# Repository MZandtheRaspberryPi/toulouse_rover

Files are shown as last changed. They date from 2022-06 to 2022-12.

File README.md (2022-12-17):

# auto_rover

this was a fun project where I made a wheeled ros based robot from scratch, including hardware, design, and substantial software for kinematics, control, and odometry (though I used existing SLAM and path planning packages).
frontal_pic

this robot has support for differential drive (with 2 driven wheels), skid steering (with 4 driven wheels), and omni wheels.

This repo is structured as a catkin workspace, so you should just clone it with submodules, and use catkin to build the workspace. Then the main entry point is:  

```
roslaunch toulouse_rover toulouse.launch wheel_config_type:=differential_drive autonomous_mode:=false
```

For autonomous mode, i often used screen as a multi-terminal utility:

```
screen -d -m -S toul -L roslaunch toulouse_rover toulouse.launch autonomous_mode:=true wheel_config_type:=fixed_pwm_speeds
```

You can find a compressed bag demo in the root of this repo, `toulouse_autonomy_demo.bag` which shows a scene of me controlling the robot and sending it forward and then turning a bit. You can also find the log outputs of this run in the root of this repo, `toulouse_autonomy.log`.  

## Demo GIFs

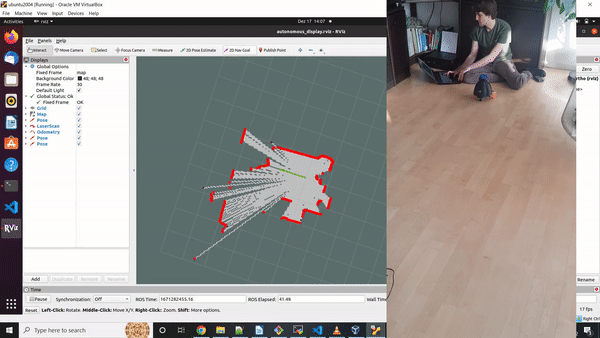
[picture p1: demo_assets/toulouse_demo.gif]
demo


## Software

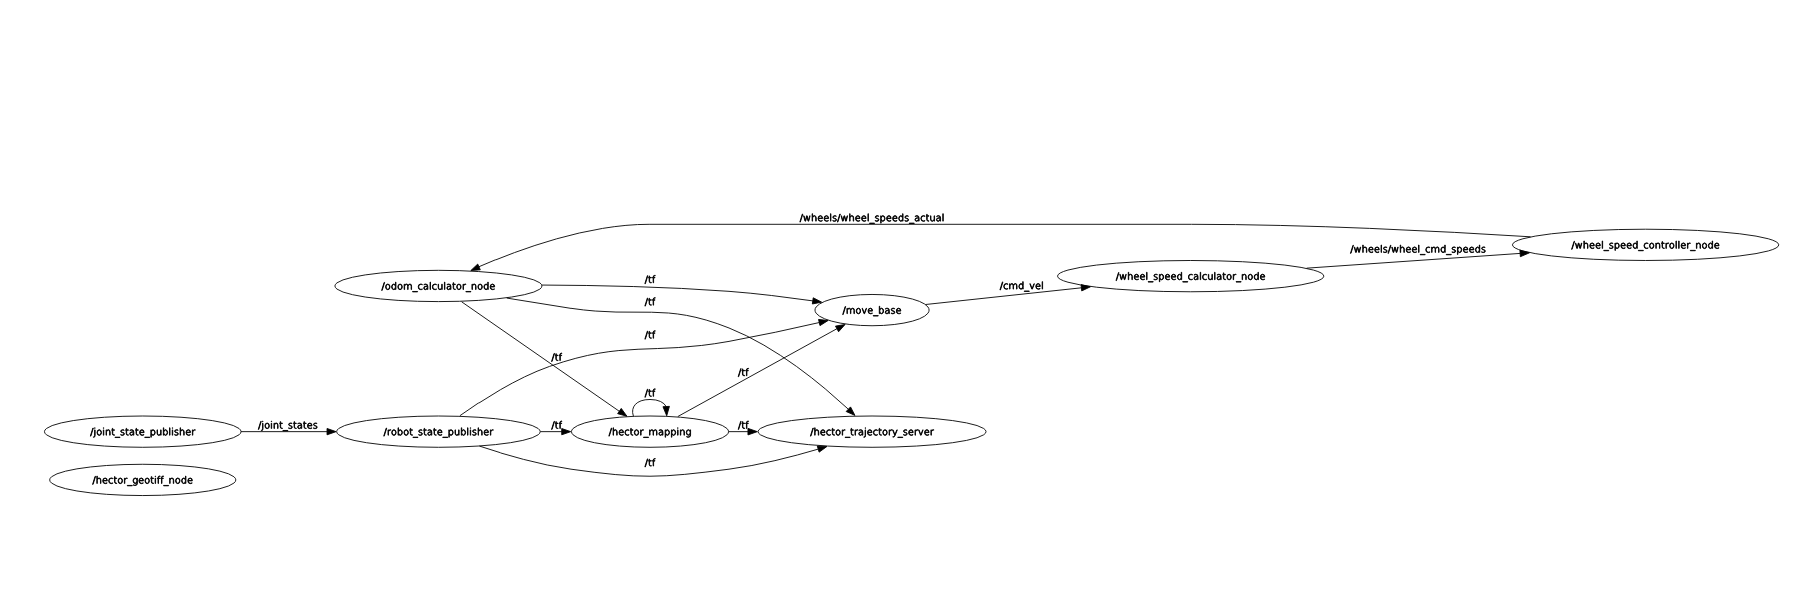
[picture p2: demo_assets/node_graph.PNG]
node_graph
  
Not pictured above is the lidar or the serial communicator node with the arduino.

You can run tests with:  

```
catkin_make run_tests toulouse_rover
```

I wrote software to do kinematics for the robot and calculate which speed wheels should turn out [WheelSpeedCalculator](src/toulouse_rover/include/toulouse_rover/wheel_speed_calculator.h) .  

I also wrote software to control the wheel speeds given encoder input, or to control the wheel speeds using a linear model to scale input from max to minimum speed [WheelSpeedController](src/toulouse_rover/include/toulouse_rover/wheel_speed_controller.h)).

I also wrote software to calculate robot position given the wheel rotation speeds, for example from encoder inputs [OdomCalculator](src/toulouse_rover/include/toulouse_rover/odom_calculator.h). I didnt end up using this as my encoders only had 20 ticks per revolution and I found it challenging to get the time step down enough to where I could rely on the output position.

The WheelSpeedCalculator listens to command velocities and then calculates what speeds wheels should turn. It then sends this to the WheelSpeedController, which calculates pwm speeds and sends this to an arduino that interfaces with the motor driver. The arduino sends the encoder data back, and this gets passed to the OdomCalculator.

I dont use the values published from OdomCalculator, instead I use Hector SLAM to publish odometry and map the room, and I use move_base to do path planning based on that. I publish command positions using rviz, and move_base publishes command velocities to achieve the goal pose.

You can find the ros package for toulouse [here](src/toulouse_rover/).

## Hardware

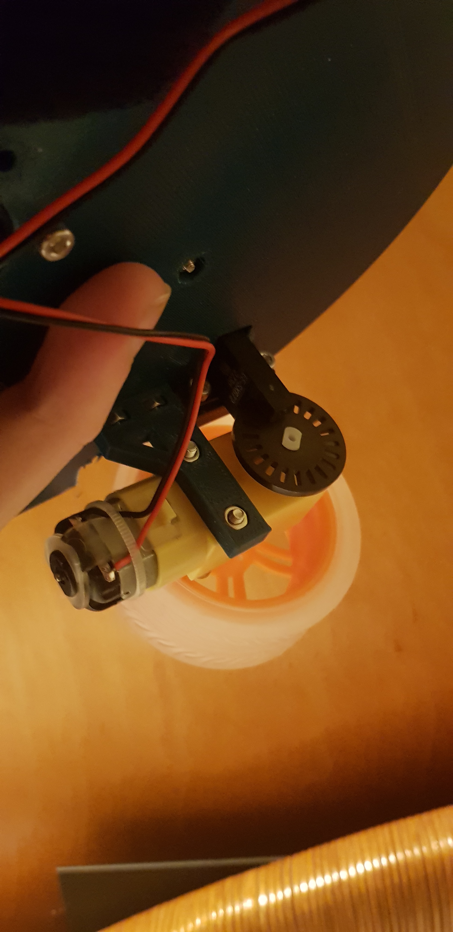
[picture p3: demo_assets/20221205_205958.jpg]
wheel_hardware
  
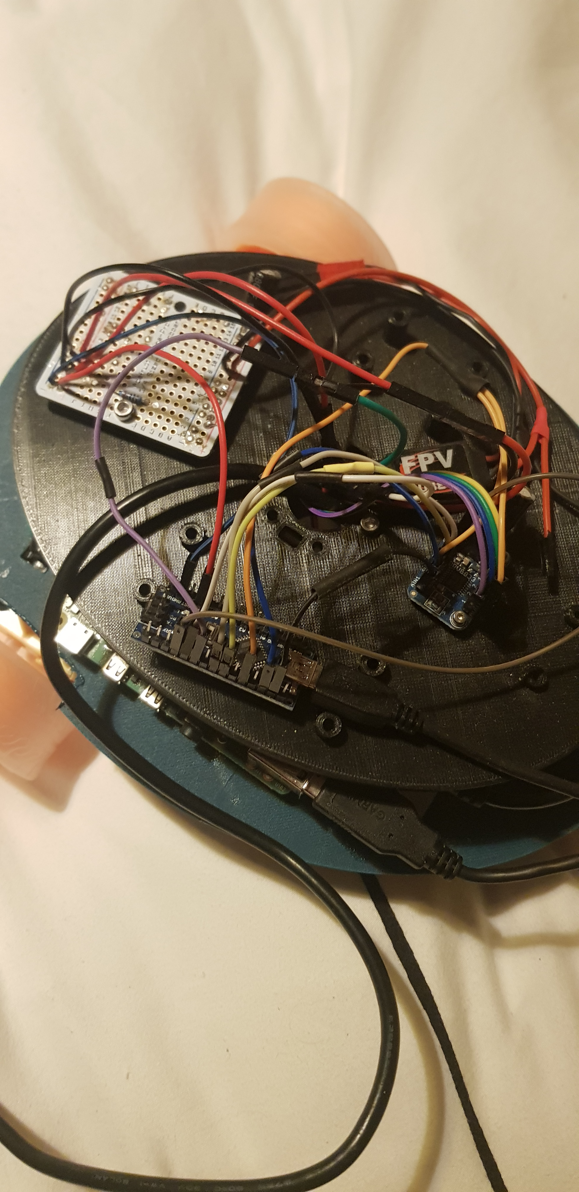
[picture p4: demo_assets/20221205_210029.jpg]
upper_hardware


The basic hardware is all from Adafruit. The motors are yellow plastic TT Motors [here](https://www.adafruit.com/product/3777) and the motor drivers are dev boards based on the DRV8833 motor driver [here](https://www.adafruit.com/product/3297). This is all powered with a 2s LIPO at 7.4 volts, with two step down converters, one to the pi, one to the motors. The encoders are plastic encoder wheels with 20 ticks per rotation. A T slot IR interupt sensor was used to measure encoder ticks.

The brains is a Raspberry PI 4 with 4gb RAM, running ubuntu 20.04.

An Arduino Nano is used to measure the interupts from the IR sensor, as well as to send PWM to the motor driver boards. It talks to the Raspberry PI via Serial.

## Design

I wanted to build a robot with wheels, as I hadnt worked with them a lot. From there I did some sketches, and it evolved into a turtle robot with a lidar on its shell, with stacked layers inside letting me mount different electronics:
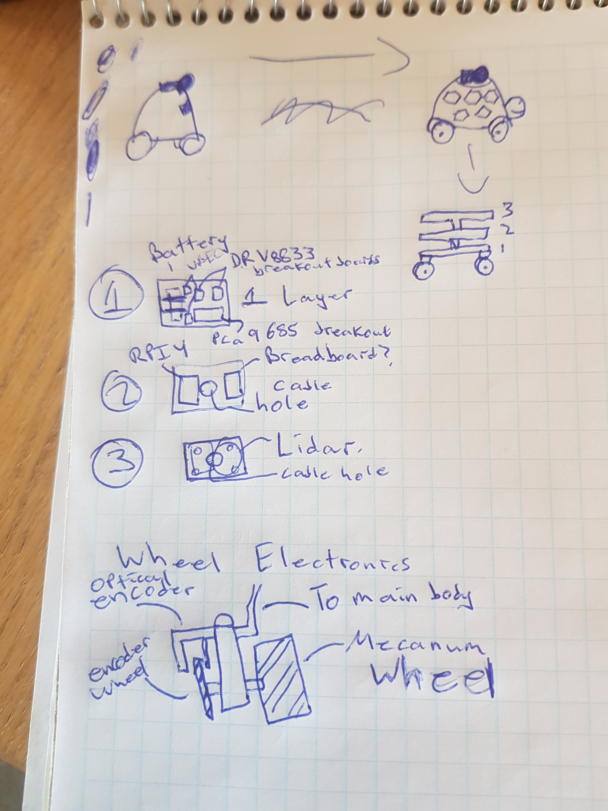
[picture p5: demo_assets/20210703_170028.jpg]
original_drawing


I tried to figure out what I would need on each layer, and what components I wanted to use for electronics. From here I started doing sketches in fusion 360...

I eventually had a full design with a turtle:
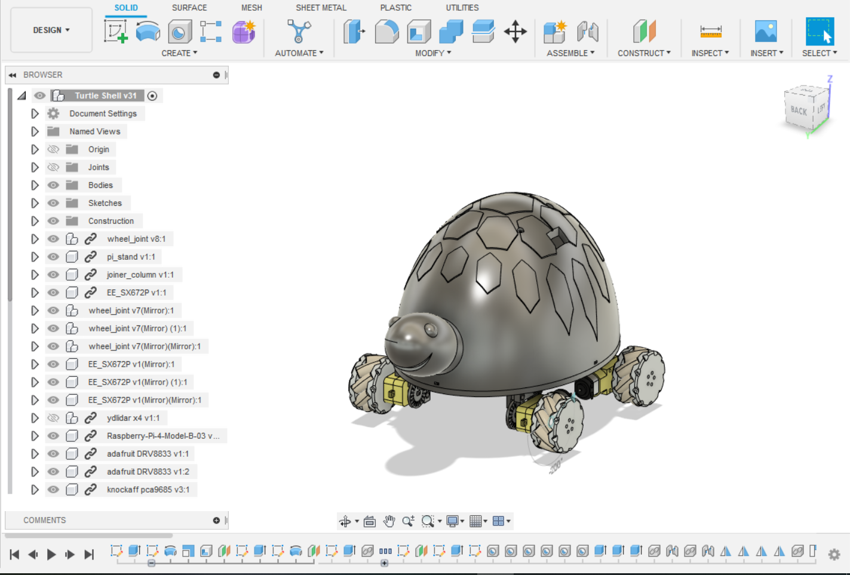
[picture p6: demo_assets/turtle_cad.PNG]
full_turtle_cad
.

And all the electronics were hidden behind the shell:
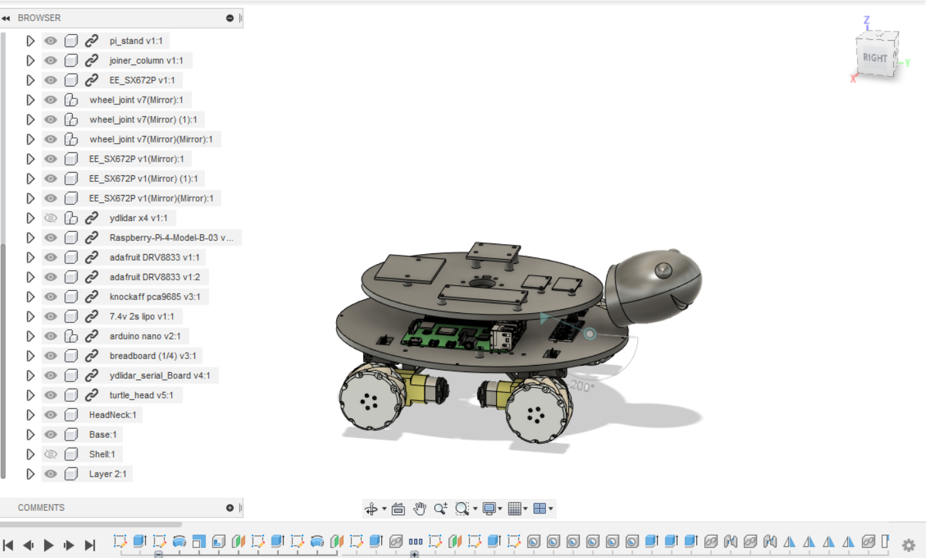
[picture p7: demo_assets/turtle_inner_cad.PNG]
inner_turtle_cad
.

You can find cad files [here](cad).

### Lessons Learned

This robot doesnt work well in autonomous mode. It was a good learning experience, but far from an end product...

## Odometry

I made some early decisions on hardware for odometry that came back to bite me...For example, the ir sensors I am using measure interupts in the path of the ir light, and the wheels with holes in them i use to interupt the ir sensor only have 20 ticks per rotation. This is challenging to use for odometry because if my motors are doing 2 revolutions per second, i get 40 ticks per second. There is noise to all sensors, including my ir sensors, and if I sample those 40 ticks per second 10 times a second, I get 4 ticks per sample. If both wheels are turning at roughly the same speed, i could still see cases where i get 3 ticks on my left wheel, and 5 on the other due to sensor noise or sampling noise. When I input this into my odometry i get pretty bad errors as it thinks the robot is turning to the left for that time frame. I eventually just used Lidar Odometry from the hector_slam package. In the future, I would use motors with built in magnetic encoders to help me with direction of the wheel spin, and also ensure high enough resolution encoders to use for odometry.

The other aspect is that with such low resolution on my encoders, I found speed control of my motors to be challenging. I would like to use the encoders to also control how fast my wheels are turning, so the magnetic encoders with higher resolution should help with that in the future.

## Front Wheel
The front wheeel I had on the rover was pretty sturdy and given my motors were weak i could actually get thrown off my course by it. For example if the wheel was pointing left and i tried to go forward, my robot would tilt forward left instead of straight forward.

To fix this, I could use a gearing system on my current motors to give them more torque and slow them down, or use different motors or a different front wheel, like a ball one.

## Lidar Power Consumption

It takes a substantial amount of current to start the Lidar spinning and my raspberry pi cant deliver that from its USB 3.0 socket. I ended up plugging in a portable power bank, like the kind you use to recharge your phone, at startup so that the lidar could draw off of that. Then I unplugged the power bank once the lidar was spinning to run autonomously. I'd like to design a better power system that can handle the lidar current, and also has some safety measures built in like monitoring the Lipo and shutting down if the battery is too low.

## Better Cable Connections

I used mostly dupont cables in this project, which come unconnected quite easily. I'd like to switch to jxt or something that stays connected and is similarly easy to unplug and re-plug.  

## More support for wheels
The way I designed the wheels, they only were attached to the body by a thin strip of plastic running in the plane from forward to backward. The wheels started to bow outward under the weight of the robot. I would design a better bracing system for the wheels that braced them forward backward as well as side to side, and perhaps connected them to each other.

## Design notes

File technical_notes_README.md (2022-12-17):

# auto_rover

a repository for a Pi4 based autonomous rover running ROS

## TODO

do documentation
figure out why when we turn robot real time lidar data stops aligning wtih the map
figure out why we cant autonomously navigate, robot just get stuck (probs above issue)

## Structure

A node that listens to cmd vel and calculates each wheels needed speed according to kinematics model and wheel configuration, and publishes it in radians per second.

One node that is listening to command wheels speeds and wheel encoder counts and using pid controllers or linear approximation to calculate the pwm to send to motor driver.

One node that is listening to wheel encoder counts and takes the wheel configuration, and calculates odometry.

Ros Navigation Stack. Ydlidar.

## Setup the Pi

There are some gotcha's in setting up Ubuntu 20.04 on the Pi4, namely trying to do it headless and dealing w/ the WiFi woes. See the section on this github and set it up accordingly. <https://github.com/MZandtheRaspberryPi/pi_headless_setup#setting-up-ubuntu> .

From there install ROS Noetic according to the ROS wiki: <http://wiki.ros.org/noetic/Installation/Ubuntu> . I would install ROS base onto the PI, and add the sourcing of setup.bash into your .bashrc file so that each time you load a terminal you can use ROS Noetic.  

Install wiringpi, which we will use to control GPIOs. If on a Pi4, you'll need to install from a fork of the original library as the original library is no longer maintained.

wiringpi library has since been stopped being mainted by original author, fork is here: <https://github.com/WiringPi/WiringPi>
see install directions here: <https://github.com/WiringPi/WiringPi/blob/master/INSTALL>  

To check pinouts:

```
cd ~/WiringPi
gpio readall
```

I'm still figuring out how to use it without sudo, for the individual user. When it was the original library the below was applicable:
To access GPIO pins as a normal user, follow this stack overflow: <https://askubuntu.com/questions/1230947/gpio-for-raspberry-pi-gpio-group>
Install an RPi library and add ubuntu to dailout group then reboot.

Eventually I moved away from wiringpi and ran all of the real time stuff on an arduino nano. I did have some weird bugs with udev rules I had setup for a lidar, to make a symlink to the serial port with a name. I had to remove this. Else I got these weird errors where my arduino would reset and not be found anymore. I eventually realized i start sending data without waiting for the bus to be up: <https://forums.raspberrypi.com/viewtopic.php?t=331475>  adding a `while(!Serial.available())` loop helped.

plug it and replug it, and it doesnt come back...

```
dmesg

[   52.647330] usb 1-1.4: USB disconnect, device number 5
[   52.649214] ftdi_sio ttyUSB1: FTDI USB Serial Device converter now disconnected from ttyUSB1
[   52.649313] ftdi_sio 1-1.4:1.0: device disconnected
[   55.685520] usb 1-1.3: new full-speed USB device number 6 using xhci_hcd
[   55.766008] usb 1-1.3: Device not responding to setup address.
[   55.973750] usb 1-1.3: Device not responding to setup address.
[   56.181530] usb 1-1.3: device not accepting address 6, error -71
[   56.265534] usb 1-1.3: new full-speed USB device number 7 using xhci_hcd
[   56.345808] usb 1-1.3: device descriptor read/64, error -32
[   56.537736] usb 1-1.3: device descriptor read/64, error -32
[   56.650061] usb 1-1-port3: attempt power cycle
[   57.253535] usb 1-1.3: new full-speed USB device number 8 using xhci_hcd
[   57.253798] usb 1-1.3: Device not responding to setup address.
[   57.461758] usb 1-1.3: Device not responding to setup address.
[   57.669535] usb 1-1.3: device not accepting address 8, error -71
[   57.753509] usb 1-1.3: new full-speed USB device number 9 using xhci_hcd
[   57.753771] usb 1-1.3: Device not responding to setup address.
[   57.961807] usb 1-1.3: Device not responding to setup address.
[   58.169537] usb 1-1.3: device not accepting address 9, error -71
[   58.176208] usb 1-1-port3: unable to enumerate USB device
```

and

```
ftdi_sio ttyUSB1: usb_serial_generic_read_bulk_callback - urb stopped: -32
```

In terms of controlling DC motors compile and run:

```
g++ -g test_motors.cpp -o test_motors -lwiringPi
sudo ./test_motor
```

For a refresher on gpio pins, navigate to where you saved WiringPi
ubuntu@ubuntu:~/WiringPi/gpio$ sudo ./gpio readall

For some thoughts on controlling many PWM from a raspberry pi, see the below. For real time operation, folks recommend a PWM driver board and communicating w/ that board via I2C.
<https://raspberrypi.stackexchange.com/questions/298/can-i-use-the-gpio-for-pulse-width-modulation-pwm> link on suggestions about control

## Wiring

For the voltage divider to get 3.3v power: <https://randomnerdtutorials.com/how-to-level-shift-5v-to-3-3v/>  
Voltage divider to go from 5v to 3.3:
Vout = Vin * R1 / (R1 + R2)
One solution is R1 = 1000 ohm, R2 = 2000 ohms

For the pullup resistor for listening to Optical Encoders: <https://learn.sparkfun.com/tutorials/pull-up-resistors/all?print=1>  

For monitoring the lipo voltage:
<https://www.instructables.com/1S-6S-Battery-Voltage-Monitor-ROS/>  
Where we use a voltage divider, but tailored to get half of total voltage for our 2s Lipo.

## uploading to arduino

we will use arduino cli for this <https://github.com/arduino/arduino-cli>.

```
curl -fsSL https://raw.githubusercontent.com/arduino/arduino-cli/master/install.sh | sh
```

<https://arduino.github.io/arduino-cli/latest/getting-started/> for intro commands
arduino:avr:nano is fqbn string for nano. can use core install arduino:avr.

add ros to 3rd party lib:
~/.arduino15$ nano arduino-cli.yaml

install rosserial arduino
<http://wiki.ros.org/rosserial_arduino/Tutorials/Arduino%20IDE%20Setup>

on newest arduino lib ros
<https://answers.ros.org/question/361930/rosserial-arduino-compilation-error-no-cstring/>  

for rosserial commands: <http://wiki.ros.org/rosserial_python>  
sudo apt-get install ros-noetic-rosserial  
rostopic echo /battery_state
screen -dmS batt rosrun rosserial_python serial_node.py _port:=/dev/ttyUSB0_baud:=57600

Batter voltage monitor: <https://www.instructables.com/1S-6S-Battery-Voltage-Monitor-ROS/>
Bug for batt voltage: <https://bugzilla.kernel.org/show_bug.cgi?id=46201>

## For the motors

To build catkin package, make sure you have build tools installed.  
sudo apt-get update && sudo apt-get install build-essential

Init submodules

```
git submodule init
git submodule update
```

```
cd ~/toulouse_rover
catkin_make
```

<https://gitlab.com/bradanlane/ros-i2cpwmboard.git>
git submodule add <https://gitlab.com/bradanlane/ros-i2cpwmboard.git> src/ros-i2cpwmboard

sudo apt-get install libi2c-dev  

sudo usermod -a -G i2c ubuntu  
sudo usermod -a -G dialout ubuntu  
sudo usermod -a -G tty $USER  

Suggestion on gpio stuff.
chown -R root:dialout /sys/class/gpio && chmod -R 770 /sys/class/gpio;
<https://answers.ros.org/question/216441/raspberry-pi-2-ros-and-gpio-access/>

guide on how to include WiringPi (namely add -lwiringPi to executable in CMakeLists and also add in some stuff to check if on windows and such).
<https://roboticsbackend.com/use-and-compile-wiringpi-with-ros-on-raspberry-pi/>

Running the motors

```
rosrun i2cpwm_board i2cpwm_board
```

On checking if on a pi:
<https://www.raspberrypi.org/forums/viewtopic.php?t=20811>

resources i2cpwm board
<https://www.youtube.com/watch?v=iLiI_IRedhI>  
<http://bradanlane.gitlab.io/ros-i2cpwmboard/>  
<https://github.com/mike4192/spotMicro/blob/master/spot_micro_motion_cmd/src/spot_micro_motion_cmd.cpp>  
<https://github.com/tizianofiorenzani/ros_tutorials/blob/master/donkey_car/src/low_level_control.py>  

To start:
source devel/setup.bash
screen -dmS core roscore
screen -dmS batt rosrun rosserial_python serial_node.py _port:=/dev/ttyUSB0_baud:=57600
screen -dmS i2c rosrun i2cpwm_board i2cpwm_board

## Kinematics for Mecanum Wheeled Robots

<https://howtomechatronics.com/projects/arduino-mecanum-wheels-robot/>  

<http://robotsforroboticists.com/drive-kinematics/>

## Kinematics for Dif Drive Robots

<https://www.hmc.edu/lair/ARW/ARW-Lecture01-Odometry.pdf>  
To solve for odom, take arc length left wheels went, arc length right wheels went, and the arc length robot drove is equal to the average of them. Can solve for that analytically too.
<https://answers.ros.org/question/231942/computing-odometry-from-two-velocities/> also as well as <https://robohub.org/drive-kinematics-skid-steer-and-mecanum-ros-twist-included/>

<https://robotics.stackexchange.com/questions/18048/inverse-kinematics-for-differential-robot-knowing-linear-and-angular-velocities>
helpful for units

```
sudo apt-get install ros-noetic-teleop-twist-keyboard
rosrun teleop_twist_keyboard teleop_twist_keyboard.py _key_timeout:=0.6 _speed:=0.1 _turn:=0.2

```

We use these wheels, 48mm diameter: <https://www.adafruit.com/product/4679>

130mm wheel seperation length

92mm wheel seperation width  

We use these optical encoder wheels: <https://www.adafruit.com/product/3782>  with 20 slots all the way round. So 20 slots is one wheel rotation.

pre-node shutdown: <https://answers.ros.org/question/27655/what-is-the-correct-way-to-do-stuff-before-a-node-is-shutdown/>  

using ROS PID
sudo apt-get install ros-noetic-pid  

sudo apt-get install ros-noetic-rqt
sudo apt-get install ros-noetic-rqt-common-plugins

rostopic pub -1 /left_front_wheel/state std_msgs/Float64 2
rostopic echo left_front_wheel/control_effort

rostopic pub -1 /left_front_wheel/setpoint std_msgs/Float64 6

for pifi:  
<https://packages.ubiquityrobotics.com/>  add to packages
<https://github.com/rohbotics/pifi>  
<https://github.com/IntelRealSense/librealsense/issues/9506>  to add key

on toulouse_robot:  
export ROS_IP=10.42.0.1

on other PC
export ROS_MASTER_URI=<http://10.42.0.1:11311>  

I was using a pi4 on the robot running ros, then a windows laptop running an ubuntu virtual machine to visualize stuff with rviz. I had a tough time getting the two to talk to each other, virtual machine and PI4. What ended up working was setting ROS_IP env variables in the .bashrc file for both (get ip from hostname -I for example), and then in the virtual machine settings under network, setting bridged, so it gets its own ip address.

Ideas for next time:  
Use arduino or 3.3v board for interupts from encoders, battery voltage measurement, and pwm signals to motor drivers.
Serial could be interface to arduino to command it.

Internet on Pi:
<https://raspberrypi.stackexchange.com/questions/109425/ubuntu-server-18-wifi-hotspot-setup>

ROSDEP

```
sudo apt-get install python3-rosdep
sudo rosdep init
rosdep update
cd ~/toulouse_rover
rosdep install --from-paths src --ignore-src -r -y

```

## debugging run

mv screenlog.0 screenlog_20221010955pm.txt
screen -dmS bag rosbag record -a
screen -d -m -S toul -L roslaunch toulouse_rover toulouse.launch autonomous_mode:=true

Things to do differently
Higher resolution encoders (20 ticks per rotation is tough to do PID with)
Make cable connectors better. Currently dupont, but self made and some of them dont plug in too well and hold.

install lidar packages. had issues with sdk for most recent driver version (<https://github.com/YDLIDAR/ydlidar_ros_driver>).
<https://github.com/YDLIDAR/ydlidar_ros>

## Making a map

<http://wiki.ros.org/slam_gmapping/Tutorials/MappingFromLoggedData>

for gmapping:  <node pkg="gmapping" type="slam_gmapping" name="slam_gmapping" args="scan:=scan"/>

issue with power of ydlidar. Takes about an amp on spin up and my pi 4 with its power system cant provide from usb. results in other stuff in the usb ports losing power. should have seperate system for this ydlidar.

# Formating and Linting

We use google style for the clang-format, and default clang-tidy settings.

```
clang-format -style=google -dump-config > .clang-format
clang-format --style=file -i src\toulouse_rover\include\toulouse_rover\odom_calc.h
```

for clang tidy, need to know compile flags. so when building, generate .json

```
catkin_make toulouse_rover -DCMAKE_EXPORT_COMPILE_COMMANDS=ON

clang-tidy -p ./build --format-style="file" src/toulouse_rover/src/wheels.cpp
```

# Testing

```
catkin_make run_tests
```

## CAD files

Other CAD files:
cad/Shell v2.f3d
cad/Turtle Shell_Base v3.f3d
cad/turtle_head v5.f3d

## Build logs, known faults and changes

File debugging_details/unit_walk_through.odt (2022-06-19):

Speed command to be 0.1 meter per second linear x. zero rotation.

wheel_front_left = (cmd_vel_msg.linear.x -

cmd_vel_msg.angular.z * util::WHEEL_SEP_WIDTH / 2.0);

wheel_front_left =

util::convert_meters_per_sec_to_radians_per_sec(wheel_front_left);

(0.1 – 0*.092/2)

so wheel front left = 0.1 meters per second

Convert.

(meters_per_sec / WHEEL_CIRCUMFERENCE ) * 2 * M_PI ;

0.1 / 0.150768 * 2 * pi

= 4.1666 radians per second ~ .66 rotations per second

to go to pwm:

float scaled_wheel_pwm =

MIN_PWM + SLOPE_WHEEL_SPEED * (std::abs(wheel_speed) - MIN_WHEEL_SPEED);

if (scaled_wheel_pwm > MAX_PWM) {

ROS_WARN("Wheel commanded to %f pwm, capping to the max of %f",

scaled_wheel_pwm, MAX_PWM);

scaled_wheel_pwm = MAX_PWM;

}

if (wheel_speed < 0) {

scaled_wheel_pwm *= -1;

}

so 900 + (4000 – 900)/3 pi (4.166 – 0) = 2270

lets say wheel moved by 2 encoder ticks in .2 seconds

double speedRadiansPerSec =

changeEncoderCounts * 2 * M_PI / encTicksPerRotation_ /

elapsed_time_s.toSec(); // 2 pi radians is 20 encoder counts, so this

// will give us radians per second

so 2 * 2 * pi / 20 / .2 = 3.141 radians per second, which is half a rotation per second.

For odom:

float speed_radians_left = (speed_front_left + speed_back_left) / 2;

float speed_radians_right = (speed_front_right + speed_back_right) / 2;

float speed_meters_left =

util::convert_radians_per_sec_to_meters_per_sec(speed_radians_left);

float speed_meters_right =

util::convert_radians_per_sec_to_meters_per_sec(speed_radians_right);

velocities.vx = (speed_meters_left + speed_meters_right) / 2;

velocities.vy = 0;

velocities.vth =

(speed_meters_right - speed_meters_left) / util::WHEEL_SEP_WIDTH;

we would get 3.141 convert to meters per second

(radians_per_sec / (2 * M_PI)) * WHEEL_CIRCUMFERENCE;

3.141 / (2 * 3.141) * 0. 150768

= 0.075384 meters per second

x velocity about equal to 0.075384 per second

and angular would be 0 here.

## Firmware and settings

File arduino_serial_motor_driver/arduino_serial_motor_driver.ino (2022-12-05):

#define SLP_PIN 8

#define PWM_1 11
#define PWM_2 10
#define PWM_3 6
#define PWM_4 5
#define leftInteruptPin 2
#define rightInteruptPin 3

volatile byte leftInteruptCount = 0;
volatile byte rightInteruptCount = 0;
int leftPriorState = HIGH;
int rightPriorState = HIGH;

byte PWM_1_VALUE = 0;
byte PWM_2_VALUE = 0;
byte PWM_3_VALUE = 0;
byte PWM_4_VALUE = 0;
bool ENABLE_MOTOR = false;

// using SLIP protocol:
// https://en.wikipedia.org/wiki/Serial_Line_Internet_Protocol
const byte END_BYTE = 0xC0;
const byte ESC_BYTE = 0xDB;
const byte ESC_END_BYTE = 0xDC;
const byte ESC_ESC_BYTE = 0xDD;

const byte NUM_BYTES = 100;
byte receivedBytes[NUM_BYTES];
byte numReceived = 0;

boolean newDataRcv = false;
boolean newDataSnd = false;

byte sendBytes[NUM_BYTES];
byte numSend = 0;

byte transformedSendBytesBuffer[NUM_BYTES];


void recvBytesWithStartEndMarkers();
void processReceivedData();
void sendBytesWithStartAndEndMarkets();
void incrementLeftInterupt();
void incrementRightInterupt();
byte addByteToArrRemovingEscSequences(const byte& in_byte, byte* byte_arr, byte& byte_arr_size);
byte addByteToArrAddingEscSequences(const byte& in_byte, byte* byte_arr, byte& byte_arr_size);


void setup() {
  Serial.begin(57600);
  while(!Serial.available()){
          delay(1);
  }

  unsigned long start_time = millis();
  double wait_time = 1000;
  while (millis() - start_time < wait_time)
  {
    delay(1);
  }
  
  pinMode(SLP_PIN, OUTPUT);
  pinMode(PWM_1, OUTPUT);
  pinMode(PWM_2, OUTPUT);
  pinMode(PWM_3, OUTPUT);
  pinMode(PWM_4, OUTPUT);

  // ir encoder open collectors
  pinMode(leftInteruptPin, INPUT_PULLUP);
  pinMode(rightInteruptPin, INPUT_PULLUP);

  attachInterrupt(digitalPinToInterrupt(leftInteruptPin), incrementLeftInterupt, FALLING);
  attachInterrupt(digitalPinToInterrupt(rightInteruptPin), incrementRightInterupt, FALLING);

}

void loop() {
/*
  if (digitalRead(leftInteruptPin) == LOW && leftPriorState == HIGH)
  {
    leftInteruptCount++;
  }
  leftPriorState = digitalRead(leftInteruptPin);
  if (digitalRead(rightInteruptPin) == LOW && rightPriorState == HIGH)
  {
    rightInteruptCount++;
  }
  rightPriorState = digitalRead(rightInteruptPin);
  */
  recvBytesWithEndMarker();
  processReceivedData();
  sendBytesWithEndMarker();
  
  digitalWrite(SLP_PIN, ENABLE_MOTOR);
  analogWrite(PWM_1, PWM_1_VALUE);
  analogWrite(PWM_2, PWM_2_VALUE);
  analogWrite(PWM_3, PWM_3_VALUE);
  analogWrite(PWM_4, PWM_4_VALUE);
}

void recvBytesWithEndMarker() {
    static byte ndx = 0;
    byte rb;

    while (Serial.available() > 0 && newDataRcv == false) {
        rb = Serial.read();
        if (rb != END_BYTE)
        {
          addByteToArrRemovingEscSequences(rb, receivedBytes, ndx);
        }
        else
        {
          ndx = 0;
          // save to use when sending out
          numReceived = ndx;
          newDataRcv = true;
        }
    }
}

void processReceivedData() {
    if (newDataRcv == true) {
        ENABLE_MOTOR = receivedBytes[0];
        PWM_1_VALUE = receivedBytes[1];
        PWM_2_VALUE = receivedBytes[2];
        PWM_3_VALUE = receivedBytes[3];
        PWM_4_VALUE = receivedBytes[4];

        byte leftEncoderToSend = leftInteruptCount;
        leftInteruptCount = 0;
        byte rightEncoderToSend = rightInteruptCount;
        rightInteruptCount = 0;

        numSend = 0;
        sendBytes[0] = ENABLE_MOTOR;
        sendBytes[1] = PWM_1_VALUE;
        sendBytes[2] = PWM_2_VALUE;
        sendBytes[3] = PWM_3_VALUE;
        sendBytes[4] = PWM_4_VALUE;
        sendBytes[5] = leftEncoderToSend;
        sendBytes[6] = rightEncoderToSend;

        for (int i = 0; i < 7; i++)
        {
          addByteToArrAddingEscSequences(sendBytes[i], transformedSendBytesBuffer, numSend);
        }

        newDataRcv = false;
        newDataSnd = true;
    }
}

void sendBytesWithEndMarker()
{
    static byte ndxSend = 0;
   
    while (Serial.availableForWrite() > 0 && newDataSnd == true) {

        if (ndxSend < numSend)
        {
          Serial.write(transformedSendBytesBuffer[ndxSend]);
          ndxSend++;
        }
        else
        {
          Serial.write(END_BYTE);
          ndxSend = 0;
          newDataSnd = false;
        }
    }
}

void incrementLeftInterupt()
{
  leftInteruptCount++;
}
void incrementRightInterupt()
{
  rightInteruptCount++;
}

byte addByteToArrRemovingEscSequences(const byte& in_byte, byte* byte_arr, byte& byte_arr_size)
{
  if (byte_arr_size >= NUM_BYTES)
  {
    // overwrite last piece of data
    byte_arr_size--;
  }

  // if we had an escape sequence before this byte, it could be
  // special
  if (byte_arr_size > 1 && byte_arr[byte_arr_size - 1] == ESC_BYTE)
  {
    switch (in_byte)
    {
      case ESC_END_BYTE:
        byte_arr[byte_arr_size - 1] = END_BYTE;
        break;
      case ESC_ESC_BYTE:
        byte_arr[byte_arr_size - 1] = ESC_BYTE;
        break;
      default:
        byte_arr[byte_arr_size] = in_byte;
        byte_arr_size++;
    }   
  }
  else
  {
    byte_arr[byte_arr_size] = in_byte;
    byte_arr_size++;
  }
}


byte addByteToArrAddingEscSequences(const byte& in_byte, byte* byte_arr, byte& byte_arr_size)
{

  if (byte_arr_size >= NUM_BYTES)
  {
    // overwrite last piece of data
    byte_arr_size--;
  }

  switch (in_byte)
  {
    case END_BYTE:
      byte_arr[byte_arr_size] = ESC_BYTE;
      byte_arr_size++;
      byte_arr[byte_arr_size] = ESC_END_BYTE;
      byte_arr_size++;
      break;
    case ESC_BYTE:
      byte_arr[byte_arr_size] = ESC_BYTE;
      byte_arr_size++;
      byte_arr[byte_arr_size] = ESC_ESC_BYTE;
      byte_arr_size++;
      break;
    default:
      byte_arr[byte_arr_size] = in_byte;
      byte_arr_size++;
  }
  
}

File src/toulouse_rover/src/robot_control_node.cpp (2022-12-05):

#include <ros/ros.h>
#ifdef RPI
#include <wiringPi.h>
#endif
#include <errno.h>
#include <geometry_msgs/TransformStamped.h>
#include <geometry_msgs/Twist.h>
#include <nav_msgs/Odometry.h>
#include <std_msgs/Float64.h>
#include <stdio.h>
#include <stdlib.h>
#include <tf2/LinearMath/Quaternion.h>
#include <tf2_geometry_msgs/tf2_geometry_msgs.h>
#include <tf2_ros/transform_broadcaster.h>
#include <cmath>



#include <math.h>

#include <chrono>

#include "odom_calc.h"
#include "wheels.h"

const int LOOP_RATE = 10;

i2cpwm_board::ServoArray servo_array{};
geometry_msgs::Twist latest_vel_msg;
void velocityCallback(const geometry_msgs::Twist::ConstPtr& vel) {
  latest_vel_msg = *vel;
}

// Signal-safe flag for whether shutdown is requested
sig_atomic_t volatile g_request_shutdown = 0;

// Replacement SIGINT handler
void mySigIntHandler(int sig) { g_request_shutdown = 1; }

// Replacement "shutdown" XMLRPC callback
void shutdownCallback(XmlRpc::XmlRpcValue& params,
                      XmlRpc::XmlRpcValue& result) {
  int num_params = 0;
  if (params.getType() == XmlRpc::XmlRpcValue::TypeArray)
    num_params = params.size();
  if (num_params > 1) {
    std::string reason = params[1];
    ROS_WARN("Shutdown request received. Reason: [%s]", reason.c_str());
    g_request_shutdown = 1;  // Set flag
  }

  result = ros::xmlrpc::responseInt(1, "", 0);
}

double x = 0.0;
double y = 0.0;
double th = 0.0;


int main(int argc, char** argv) {
#ifdef RPI
  wiringPiSetup();
  pinMode(SLP_PIN, OUTPUT);
  ROS_INFO("GPIO has been set as OUTPUT.");

  digitalWrite(SLP_PIN, HIGH);
#endif
  ros::init(argc, argv, "robot_control_node",
            ros::init_options::NoSigintHandler);
  ros::NodeHandle nh;
  // Override the default ros sigint handler.
  // This must be set after the first NodeHandle is created.
  signal(SIGINT, mySigIntHandler);

  // Override XMLRPC shutdown
  ros::XMLRPCManager::instance()->unbind("shutdown");
  ros::XMLRPCManager::instance()->bind("shutdown", shutdownCallback);

  odom_calc::OdomCalculator odom_calculator{odom_calc::DIFFERENTIAL_DRIVE};

  ros::Subscriber velocity_sub_ = nh.subscribe("cmd_vel", 1, velocityCallback);
  // servos_absolute publisher
  ros::Publisher servos_absolute_pub =
      nh.advertise<i2cpwm_board::ServoArray>("servos_absolute", 1);

  ros::Rate loop_rate(LOOP_RATE);  // Control rate in Hz

  wheels::FrontLeftWheel front_left_wheel(nh, "front_left_wheel", false,
                                          odom_calc::DIFFERENTIAL_DRIVE);
  wheels::FrontRightWheel front_right_wheel(nh, "front_right_wheel", false,
                                            odom_calc::DIFFERENTIAL_DRIVE);
  wheels::BackLeftWheel back_left_wheel(nh, "back_left_wheel", false,
                                        odom_calc::DIFFERENTIAL_DRIVE);
  wheels::BackRightWheel back_right_wheel(nh, "back_right_wheel", false,
                                          odom_calc::DIFFERENTIAL_DRIVE);

#ifdef RPI
  wiringPiISR(0, INT_EDGE_FALLING, &wheels::frontLeftInterupt);
  wiringPiISR(2, INT_EDGE_FALLING, &wheels::frontRightInterupt);
  wiringPiISR(25, INT_EDGE_FALLING, &wheels::backLeftInterupt);
  wiringPiISR(3, INT_EDGE_FALLING, &wheels::backRightInterupt);
#endif

  ros::Publisher odom_pub = nh.advertise<nav_msgs::Odometry>("odom", 50);
  static tf2_ros::TransformBroadcaster br;
  geometry_msgs::TransformStamped transformStamped;
  ros::Time current_time, last_time;
  current_time = ros::Time::now();
  last_time = ros::Time::now();
  ros::Duration(1.0).sleep();

  // Initialize servo array message with 12 servo objects
  for (int i = 1; i <= 16; i++) {
    i2cpwm_board::Servo temp_servo;
    temp_servo.servo = i;
    temp_servo.value = 0;
    servo_array.servos.push_back(temp_servo);
  }
  servos_absolute_pub.publish(servo_array);
  int front_left_wheel_pwm;
  int front_right_wheel_pwm;
  int back_left_wheel_pwm;
  int back_right_wheel_pwm;
  while (!g_request_shutdown) {
    // the work...
    ROS_INFO_THROTTLE(1, "x: %f, y: %f, angl_y: %f", latest_vel_msg.linear.x,
           latest_vel_msg.linear.y, latest_vel_msg.angular.z);
    front_left_wheel_pwm = front_left_wheel.ctrlWheelCmdVel(latest_vel_msg);
    front_right_wheel_pwm =
      front_right_wheel.ctrlWheelCmdVel(latest_vel_msg);
    back_left_wheel_pwm = back_left_wheel.ctrlWheelCmdVel(latest_vel_msg);
    back_right_wheel_pwm = back_right_wheel.ctrlWheelCmdVel(latest_vel_msg);
    ROS_INFO_THROTTLE(1, "FL: %d, FR: %d, BL: %d, BR: %d", front_left_wheel_pwm,
             front_right_wheel_pwm, back_left_wheel_pwm, back_right_wheel_pwm);
    if (front_left_wheel_pwm < 0) {
      servo_array.servos[14].value = 0;
      servo_array.servos[15].value = std::abs(front_left_wheel_pwm);
    } else {
      servo_array.servos[15].value = 0;
      servo_array.servos[14].value = std::abs(front_left_wheel_pwm);
    }

    if (front_right_wheel_pwm < 0) {
      servo_array.servos[13].value = 0;
      servo_array.servos[12].value = std::abs(front_right_wheel_pwm);
    } else {
      servo_array.servos[12].value = 0;
      servo_array.servos[13].value = std::abs(front_right_wheel_pwm);
    }

    if (back_left_wheel_pwm < 0) {
      servo_array.servos[9].value = 0;
      servo_array.servos[8].value = std::abs(back_left_wheel_pwm);
    } else {
      servo_array.servos[8].value = 0;
      servo_array.servos[9].value = std::abs(back_left_wheel_pwm);
    }

    if (back_right_wheel_pwm < 0) {
      servo_array.servos[10].value = 0;
      servo_array.servos[11].value = std::abs(back_right_wheel_pwm);
    } else {
      servo_array.servos[11].value = 0;
      servo_array.servos[10].value = std::abs(back_right_wheel_pwm);
    }

    servos_absolute_pub.publish(servo_array);
    ros::spinOnce();

    // compute odometry in a typical way given the velocities of the robot
    double speed_front_left = front_left_wheel.getWheelSpeed();
    double speed_front_right = front_right_wheel.getWheelSpeed();
    double speed_back_left = back_left_wheel.getWheelSpeed();
    double speed_back_right = back_right_wheel.getWheelSpeed();

    ROS_INFO("back left wheel speed: %f", speed_back_left);

    odom_calc::Velocities velocities = odom_calculator.calc_velocities(
        speed_front_left, speed_front_right, speed_back_left, speed_back_right);

    odom_calc::PositionChange pos_change =
        odom_calculator.calc_position_change(velocities);

    odom_calc::Position position = odom_calculator.calc_position(pos_change);

    odom_calc::OdomRosMessages odom_messages =
        odom_calculator.get_ros_odom_messages(position, velocities);

    // send the transform
    br.sendTransform(odom_messages.odom_transform);

    // publish the message
    odom_pub.publish(odom_messages.odom);
    loop_rate.sleep();
  }
  for (int i = 1; i <= 16; i++) {
    servo_array.servos[i].value = 0;
  }
  servos_absolute_pub.publish(servo_array);
#ifdef RPI
  digitalWrite(SLP_PIN, LOW);
#endif
  ros::shutdown();
}

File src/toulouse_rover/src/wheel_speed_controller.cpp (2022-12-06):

#include "toulouse_rover/wheel_speed_controller.h"

namespace wheel_speed_controller
{
static volatile double globalEncCounter[4];
static volatile double globalSpeedCounter[4];

toulouse_rover::WheelPwmSpeeds getZeroPwmSpeedsMsg()
{
  toulouse_rover::WheelPwmSpeeds pwm_speeds_msg;
  pwm_speeds_msg.motor_enable = true;
  pwm_speeds_msg.front_left_pwm_1 = 0;
  pwm_speeds_msg.front_left_pwm_2 = 0;

  pwm_speeds_msg.front_right_pwm_1 = 0;
  pwm_speeds_msg.front_right_pwm_2 = 0;

  pwm_speeds_msg.back_left_pwm_1 = 0;
  pwm_speeds_msg.back_left_pwm_2 = 0;

  pwm_speeds_msg.back_right_pwm_1 = 0;
  pwm_speeds_msg.back_right_pwm_2 = 0;

  return pwm_speeds_msg;
}

// Replacement SIGINT handler
void mySigIntHandler(int sig)
{
  wheel_speed_controller::g_request_shutdown = 1;
}

// Replacement "shutdown" XMLRPC callback
void shutdownCallback(XmlRpc::XmlRpcValue& params, XmlRpc::XmlRpcValue& result)
{
  int num_params = 0;
  if (params.getType() == XmlRpc::XmlRpcValue::TypeArray)
    num_params = params.size();
  if (num_params > 1)
  {
    std::string reason = params[1];
    ROS_WARN("Shutdown request received. Reason: [%s]", reason.c_str());
    wheel_speed_controller::g_request_shutdown = 1;  // Set flag
  }

  result = ros::xmlrpc::responseInt(1, "", 0);
}

BaseWheelSpeedController::BaseWheelSpeedController(ros::NodeHandle& nh, const std::string wheel_namespace, bool use_pid,
                                                   util::WheelConfigurationType wheel_config_type)
  : wheel_namespace_(wheel_namespace), use_pid_(use_pid), wheel_config_type_(wheel_config_type)
{
  setupPubsSubs(nh, wheel_namespace_);
  priorEncoderCounts_ = 0;
  control_effort_ = 0.;
  encoderStartTime_ = ros::Time::now();

  if (use_pid_)
  {
    std::vector<std::string> nodes;
    bool found_pid_node = false;
    std::string node_to_find = wheel_namespace_ + wheel_namespace_.substr(0, wheel_namespace_.size() - 3);
    while (ros::ok() && !found_pid_node)
    {
      ros::master::getNodes(nodes);
      for (const auto& node : nodes)
      {
        if (node == node_to_find)
        {
          found_pid_node = true;
        }
      }
      ROS_DEBUG("waiting for %s", node_to_find.c_str());
      ros::Duration(0.1).sleep();
    }
  }

  is_initialized_ = true;
}

FrontLeftWheelSpeedController::FrontLeftWheelSpeedController(ros::NodeHandle& nh, std::string wheel_namespace,
                                                             bool use_pid,
                                                             util::WheelConfigurationType wheel_config_type)
  : BaseWheelSpeedController(nh, wheel_namespace, use_pid, wheel_config_type)
{
  encoderIndex_ = 0;
}
void FrontLeftWheelSpeedController::publishWheelState()
{
  BaseWheelSpeedController::publishWheelState();
}

FrontRightWheelSpeedController::FrontRightWheelSpeedController(ros::NodeHandle& nh, std::string wheel_namespace,
                                                               bool use_pid,
                                                               util::WheelConfigurationType wheel_config_type)
  : BaseWheelSpeedController(nh, wheel_namespace, use_pid, wheel_config_type)
{
  encoderIndex_ = 1;
}
void FrontRightWheelSpeedController::publishWheelState()
{
  BaseWheelSpeedController::publishWheelState();
}

BackRightWheelSpeedController::BackRightWheelSpeedController(ros::NodeHandle& nh, std::string wheel_namespace,
                                                             bool use_pid,
                                                             util::WheelConfigurationType wheel_config_type)
  : BaseWheelSpeedController(nh, wheel_namespace, use_pid, wheel_config_type)
{
  encoderIndex_ = 2;
}
void BackRightWheelSpeedController::publishWheelState()
{
  BaseWheelSpeedController::publishWheelState();
}

BackLeftWheelSpeedController::BackLeftWheelSpeedController(ros::NodeHandle& nh, std::string wheel_namespace,
                                                           bool use_pid, util::WheelConfigurationType wheel_config_type)
  : BaseWheelSpeedController(nh, wheel_namespace, use_pid, wheel_config_type)
{
  encoderIndex_ = 3;
}
void BackLeftWheelSpeedController::publishWheelState()
{
  BaseWheelSpeedController::publishWheelState();
}

void BaseWheelSpeedController::setupPubsSubs(ros::NodeHandle& nh, const std::string wheel_namespace)
{
  state_pub_ = nh.advertise<std_msgs::Float64>(wheel_namespace + "/state", 100);

  set_pub_ = nh.advertise<std_msgs::Float64>(wheel_namespace + "/setpoint", 100);
  if (use_pid_)
  {
    ctrl_sub_ =
        nh.subscribe(wheel_namespace + "/control_effort", 1, &BaseWheelSpeedController::controlEffortCallback, this);
    pid_enable_pub_ = nh.advertise<std_msgs::Bool>(wheel_namespace + "/pid_enable", 100);
    std_msgs::Bool enable_msg;
    enable_msg.data = true;
    pid_enable_pub_.publish(enable_msg);
  }
}

BaseWheelSpeedController::~BaseWheelSpeedController()
{
  if (use_pid_)
  {
    /*
    std_msgs::Float64 state;
    state.data = 0.0;
    state_pub_.publish(state);
    ros::spinOnce();
*/
    std_msgs::Bool enable_msg;
    enable_msg.data = false;
    pid_enable_pub_.publish(enable_msg);
  }
}

void BaseWheelSpeedController::controlEffortCallback(const std_msgs::Float64& control_effort_input)
{
  ROS_DEBUG("got ctrl effort %s %f", wheel_namespace_.c_str(), control_effort_input.data);
  const std::lock_guard<std::mutex> lock(control_effort_mutex_);
  control_effort_ = control_effort_input.data;
  got_control_data_ = true;
}

bool BaseWheelSpeedController::getControlEffort(float& control_effort)
{
  const std::lock_guard<std::mutex> lock(control_effort_mutex_);
  if (got_control_data_)
  {
    control_effort = control_effort_;
    got_control_data_ = false;
    // TODO: Figure out why PID node sometimes publishes zero, even when it shouldnt.
    if (control_effort == 0.)
    {
      return false;
    }
    return true;
  }
  else
  {
    return false;
  }
}
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

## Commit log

2021-10-08 updating to give motors example
2021-10-08 updating example for all four motors
2021-10-12 encoders working and wheels working
2021-10-12 making kinematics
2021-10-12 starting to update for kinematics
2021-10-23 testing for ir interupt issue
    [test_motors_ros.cpp]
2021-10-23 first draft of wheel encoder controller
2021-10-23 adding pid
2021-10-30 testing pid for motor control
2021-10-31 adding monitoring node to help tune pid controllers
2021-11-20 draft of wheel control
2021-11-27 updates to not use pid
2021-11-27 enabling motors
2021-11-27 doing save shutdown motors
2021-11-27 fixing bug for left motors
    [robot_control_node.cpp]
2021-12-12 adding urdf file@
    [toulouse.urdf]
2021-12-12 adding files for mapping
    [toulouse.urdf.xacro]
2021-12-12 adding lidar to launch file
2021-12-12 getting slam up using dynamic map
    [toulouse.urdf.xacro]
2022-01-30 adding submodule, putting sim mode in, capping pwm
2022-04-26 updating config files
    [toulouse.urdf.xacro]
2022-04-26 adding battery monitor to roslaunch
2022-06-16 fixing left/right synch bug
    [robot_control_node.cpp]
2022-06-16 updating wheel radius to be new wheels
2022-06-18 adding two wheel option
2022-06-18 ensuring front wheels dont move when in diff drive mode
2022-07-16 updating to do mapping
    [toulouse.urdf.xacro]
2022-08-27 updating format file to ros, fixing build issues
    [util.cpp, util.h, wheel_speed_controller.cpp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]
2022-10-03 renaming some wheel topics
2022-10-03 adding python serial driver node
2022-10-03 putting a min pwm in
2022-10-03 fixing serial print driver
    [serial_motor_driver.py]
2022-10-03 adding arduino driver
2022-10-04 outputting serial node to screen, bug in control
    [wheel_speed_controller.cpp]
2022-10-05 updating logic of serial driver
2022-10-05 updating logic to slip
    [arduino_serial_motor_driver.ino]
2022-10-08 doing raw encoder publishing with data from arduino
2022-10-08 adding arduino fix
2022-10-09 fixing bug using unitted stuff
    [wheel_speed_controller.cpp]
2022-10-09 updating scaling on the pwm
2022-10-09 bounding encoder counts
2022-10-10 updating arduino to wait a bit before sending data
2022-10-10 updating max and min velocities for planner
2022-10-10 adding param for serial port for lidar
2022-10-10 removing reference to pwmboard
2022-10-10 updating max encoder ticks
2022-10-10 lowering map updates, adding force refresh for encoders before state pub
2022-10-10 adding more filtering to encoder data
2022-12-05 updating documentation
    [Shell v2.f3d, Turtle Shell_Base v3.f3d, turtle_head v5.f3d]
2022-12-06 first draft fixed rates
    [wheel_speed_controller_params.yaml]
2022-12-06 updating params, bug fixes for new mode
    [wheel_speed_controller_params.yaml]
2022-12-17 updating fixed speeds
    [wheel_speed_controller_params.yaml]
2022-12-17 adding note on front wheel
